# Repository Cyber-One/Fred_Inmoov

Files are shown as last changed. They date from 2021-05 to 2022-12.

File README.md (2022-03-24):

# Fred_Inmoov #


Frequently Re-Engineered Device (FRED)
Fred is a modified InMoov Robot.
You can find the videos showing his contruction here:
https://youtube.com/playlist?list=PLgXTfFM40HqEbnFfhaLPmLv_RS1ZRCilI

In the Official build of InMoov, http://inmoov.fr/
there are two Arduino Mega 2560's located on his back with the I/O distributed using the Nervo Boards available from the online shop in the Inmoov website.
There was also a 8" Lenovo Windows based tablet that running the Java based MyRobotLab http://myrobotlab.org/ that remotely operated the two Arduino Mega 2560's

Because I like to be different, I used the PCA9685 I2C 16 channel PWM driver boards based on the Adafruit servo driver breakout board.
4 of these in various places throughout the robot provide the servo control while reducing the nuber of wires running about the robot.

Lets look at Fred in more detail.
Snapshot - 8

The head is where most of the modifications have been made.
The large Hitech 805BB servo was replaced by a smaller JX Servo PDI6221MG and moved to the back of the skull and turned sideways.
The Jaw servo was relocated turning it over and also moving it sideways.
The eye mechanism was replace with the Dakota76 Advance Eye Mechanism, this has 6 servos with upper and lower eye lids.
With the changes made, there is now enough room in the skull for a Raspberry Pi 4, a PCA9685 Servo Driver and two Switched mode Power Supplies (SMPS) dropping the 20Vdc main power supply down to the 6V for the PCA9685 and 5,1V for the Raspberry Pi.

I used the new neck from the Inmoov.fr site by Gael, this one is far stronger that the other derivative from bob Houstons articultaed neck design.
The downside was because of the modified jaw design and the placement of the SMPS for the PCA9685, I had to extent up the neck mount a bit.
The result is a bit taller neck than normal, this adds close to an inch of height.

Another PCA9685 is located in the back to driver the servos in this area.
Because a lot of these servos are of the larger type, I've used a 20A SMPA to drop the 20Vdc to the 6Vdc for the servos.
I also have a smaller 3A SMPS to power a small 5 port network switch and a second Raspberry Pi located on the back of a 7" LCD touch screen mounted where the original 8" tablet was.


I will be adding two more 20A SMPS, one in each arm to power the servos in the elbow and hands.

One of the most common questions I get about Fred is why am I using 20Vdc in his power system.
The answer to this is to avoid as much power loss as I can.
Power = Volts x Amps.
Volts = Amps x resistance.
Power = Resistance x Amps X Amps.
What a lot of people don't understand is that all wire has a resistance, granted its normally very low, but its there.
The larger the diameter the wire, the lower the resistance, but the longer the wire, the higher the resistance.
If you have a current flowing through a resistance, Ohms Law states there will be a voltage across that resistance.
If you multiply the voltage with the amps flowing you get the power lost in that resistance.  This is power loss.
If you have a servo running 6Vdc at 2.5 Amps, it will be consuming 15 watts of power. 
If you have small wires running a sizable distance you can get quite a voltage drop in the power wires feeding the servo, enough to drop your 6V supply down to 5V or less at the servo this is a 2.5 Watt loss in power that your servo is not getting.
To complicate the matter further, motors will automatically adjust there impedance (think of this as a changing resistance) to get the power they need to rotate the load.
So if the voltage drops, then the motor needs to increase the current to get the same power.
If the impedance drops to the resistance of the servo and there is still not enough power to turn the motor, the result will be a burned out servo motor.
To overcome this problem, I'm keeping the length of the 6Vdc low voltage supply as short as possible, resuding the resistance of those power wires. (Shorter wires, lower resistance, less power lost)
Using a higher voltage, means a lower current for the same amount of power.
At 20Vdc, I end up with 1/3 the amount of current flowing in the supply wires running throught the robot. 
Because the power lost is the wire resistance x Amps squared, that works out to be a significant power saving.
It also means the wires don't have to be overly large.  
Bigger wires also weight more and are not as flexiable.
So there are a few benifits to a higher voltage distribution system.
There is a good table for wire sizes, current capacity and the resistance of the wires at Wikipedia here:
https://en.wikipedia.org/wiki/American_wire_gauge#Tables_of_AWG_wire_sizes

In version 5 of the program I'm using to run Fred, I split the single script up into a number of files and expanded on the comments to help better explain what is happening.
With a bit of luck you will be able to follow along and learn more about how MRL works.
All of the programming I've done is in Python which will make it easier if you want to use this program and need to add to it.

If you have any questions regarding any of the files here, drop into my Discord and ask your questions, hopefully I will be able to answer the questions or implement changes if needed. :-)
https://discord.gg/WzrBUTkthQ

You can download the latest development version of MRL from the MRL website, while your there don't forget to say hello to the developers in the shoutbox.
http://myrobotlab.org/

If your would like to help support this project, then consider Patreon

<a href="https://www.patreon.com/bePatron?u=10744269">Digital-Patreon-Wordmark_WhiteOnFieryCoral-Lg
</a>

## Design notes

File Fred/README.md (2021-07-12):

# Fred Inmoov V5.0 program

Unlike earlier version of Fred's program, this one has split the program up into different sections to make it easier to find parts.
It may yet be broken up into more modular files.
Breaking the project up into a smaller files makes it easier to find and debug issue.
It also helps with designing new features.

Where possible, lots of comment have been placed in the code to help NOOB's learn how MyRobotLab services work and how this section is supposed to work. :-)
It can be advantagous when your trying to use service if you can look up and see how it's ment to be called as well.

<b>Start.py </b>
General start point and is responsible for starting the Graphical User Interface (GUI) and calling all the other sub files required to start up the system.

<b>1_Configuration/</b>
This Folder is where the various configuration files are stored for Fred.
If you are using these scripts for your robot, then this is where you change the config to suit your build.
I've tried to add notes as to what each of the setting do.

<b>Controller.py </b>
This is where the top level controllers are created such as the RasPi service, the Arduino services and the PCA9685 services.

<b>3_Servos/</b>
Because there are so many servos used in an Inmoov build and a modified one like Fred use even more, the servos service creation is broken into multiple files.
I've tried to group servos by physical area of operation, not controller or location of the servo.
For example, the Neck group contains the head Roll, Pitch and Yaw servos, the Roll and Pitch are located below the neck while the Yaw is located in the head. 

<b>IO.py</b>
This is for miscilanous IO devices like the PIR sensor and the Ultrasonic range finders.

<b>Speech.py</br>
This is where the Text To Speech and Speech recognition services are created.

<b>Life.py</b>
This set of routines control the simulation of being alive like the blinking of the eye lids and random movements that simulate a living being.
Because the Life Simulation functions are so complex (mostly to support different types of build) a sub folder was created to break the life functions down into groups of functions.
Later functions will call in and control lower level functions so as to make coordinated moves, like moving the eyes and head to look at an object.

<b>Gestures.py</b>
Any scripts of movements such as shaking the head as a no, or nodding the head as a yes, that may be called by the ProgramAB are scripted here.
Think of the Life functions as involuntary functions and Gestures as voluntary functions, normally called from the brain (ProgramAB)

<b>Brain.py</b>
This is where the simulated AI lives. :-)
For now, this is ProgramAB, a program that runs Artificial Inteligents Markup Language (AIML) files commonly refered to as Alice Bot.

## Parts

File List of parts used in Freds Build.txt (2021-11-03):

I get asked a lot about where I get the STL files I used in the building of Fred.
Below is a list of the different locations for parts I've printed that are non-standard Inmoov parts.
All other parts not listed are on the official Inmoov site
http://www.inmoov.fr/

https://www.thingiverse.com/thing:2394098
InMoov - Accessible skull with continous forehead by dix238.

http://www.thingiverse.com/thing:992918
Modified InMoov head by monnerby.

http://www.thingiverse.com/thing:3395654
InMoov Neck Head Bracket Another Redesign v2 by richardtracy

http://www.thingiverse.com/thing:2335838
InMoov LowBackSkull & Gear remix by richardtracy

http://www.thingiverse.com/thing:1581955
InMoov - Low Back Skull / Neck Joint - Modification by dix23.

https://www.thingiverse.com/thing:1636086
InMoov Face less holes by juergm.

http://www.thingiverse.com/thing:2062472
Raspberry Pi 2 Stacking System by TafThorne
This was modified to let me use PCB standoffs.

https://www.thingiverse.com/thing:2548952
InMoov - Advanced Eye Mechanism by Dakota76.

Alexinator40
Remixed from
http://www.thingiverse.com/thing:3395654
InMoov Neck Head Bracket Another Redesign v2 by richardtracy
Remixed from
http://www.thingiverse.com/thing:1581955
InMoov - Low Back Skull / Neck Joint - Modification by dix23
Remixed from
http://www.thingiverse.com/thing:992918
Modified InMoov head by monnerby.
Remixed from
http://www.inmoov.fr/
Created by Gael Langevin

AT30_SMPS.STL https://www.dropbox.com/s/qasvv97k4j6kot5/AT30_SMPS.stl?dl=0
Created by Cycber_One

PCA9685_Mount.STL https://www.dropbox.com/s/vjgidlmbo2zt9v8/PCA9685_Mount.stl?dl=0
Created by Cyber_One

http://www.thingiverse.com/thing:2770920
Aldi Xfinity and Ryobi (south africa) battery connector by Stoney

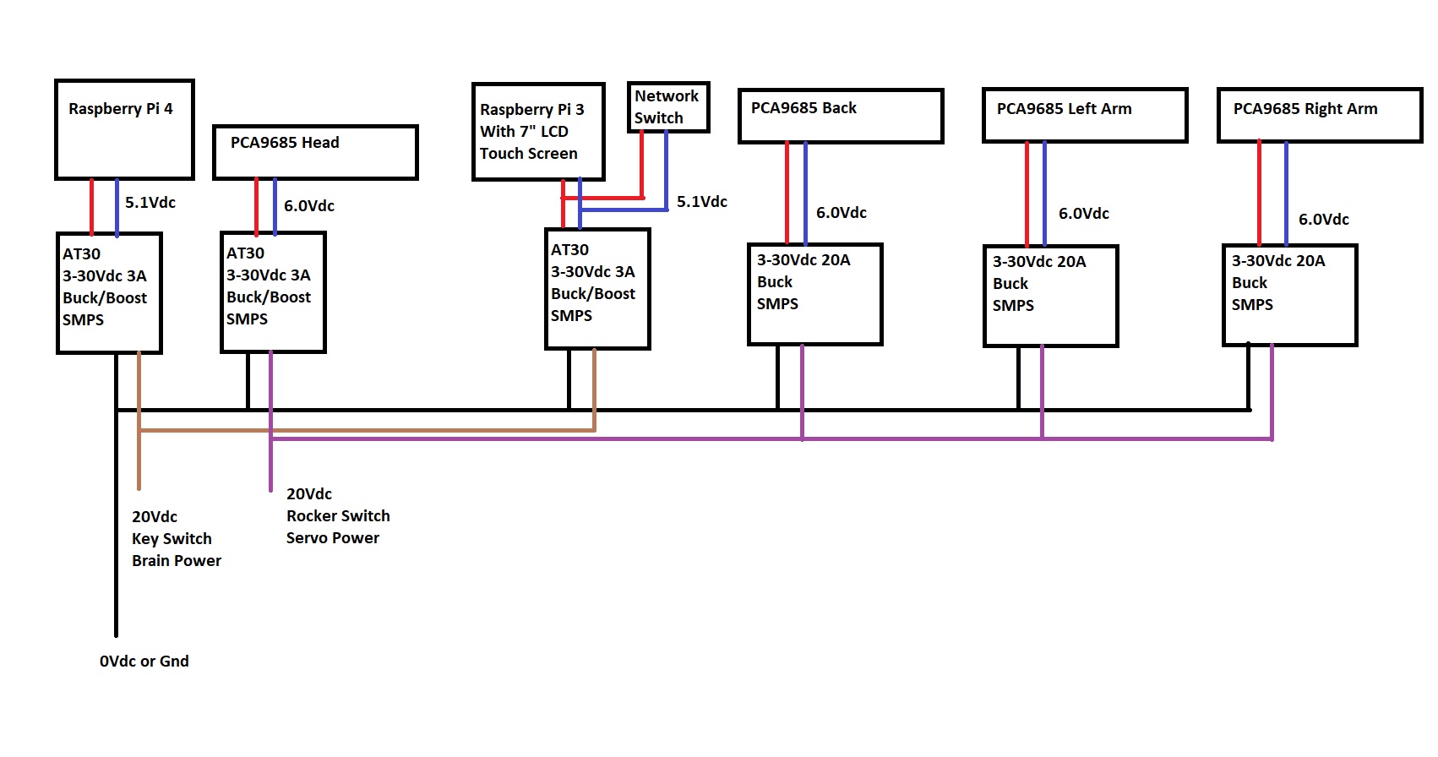
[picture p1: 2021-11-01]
Parts/Power System Layout.jpg

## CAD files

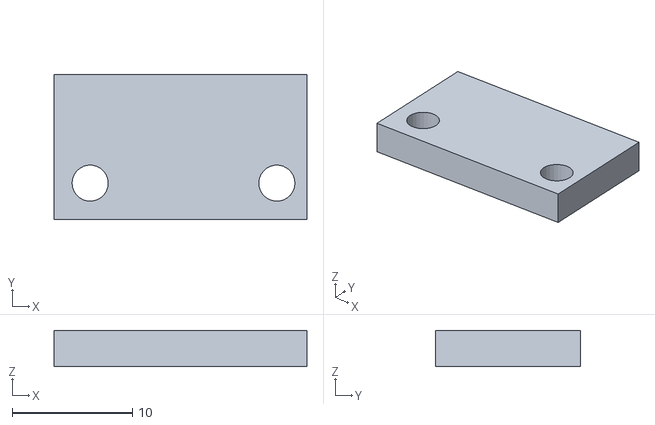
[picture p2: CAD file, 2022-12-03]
Parts/MPU6050_Mount.stl
21.0 x 12.0 x 3.00

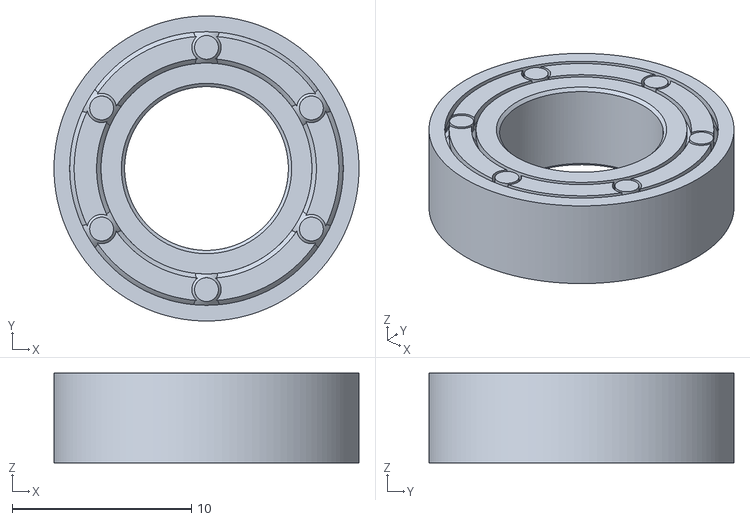
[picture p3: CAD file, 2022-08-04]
Parts/Bearing_689_Hv1_9x17x5.stl
17.0 x 17.0 x 5.00

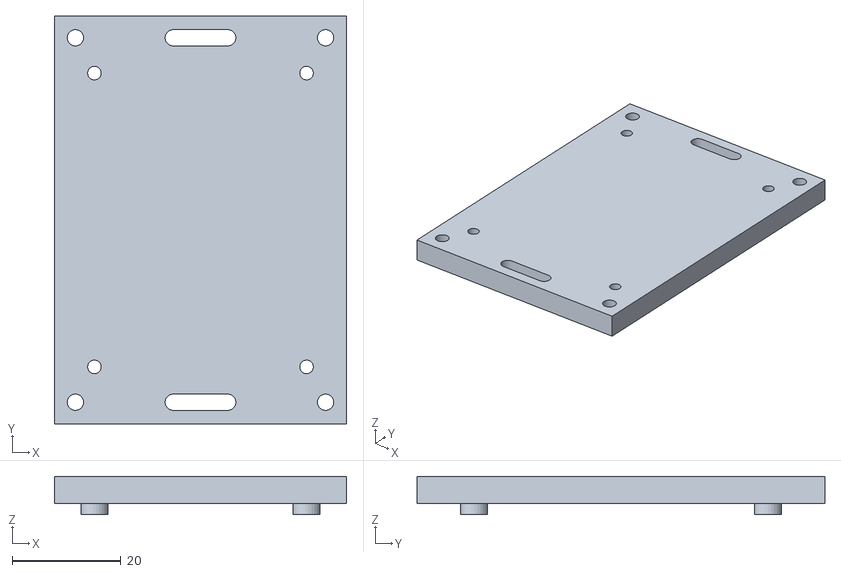
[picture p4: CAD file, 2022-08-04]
Parts/20A_SMPS_Mount_V2.stl
53.7 x 75.0 x 7.00

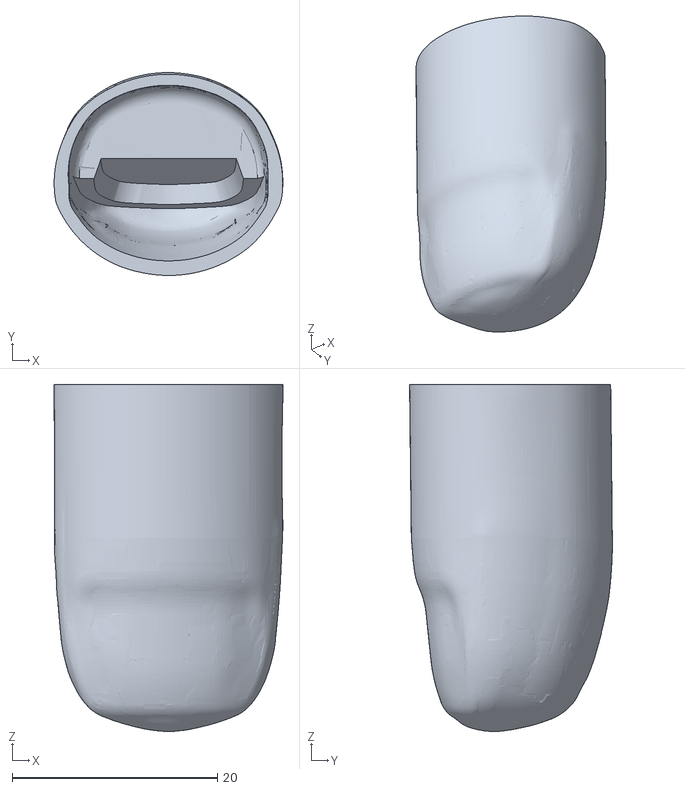
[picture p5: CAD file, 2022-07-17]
Parts/Thumb_TipV2.stl
22.3 x 19.8 x 33.8

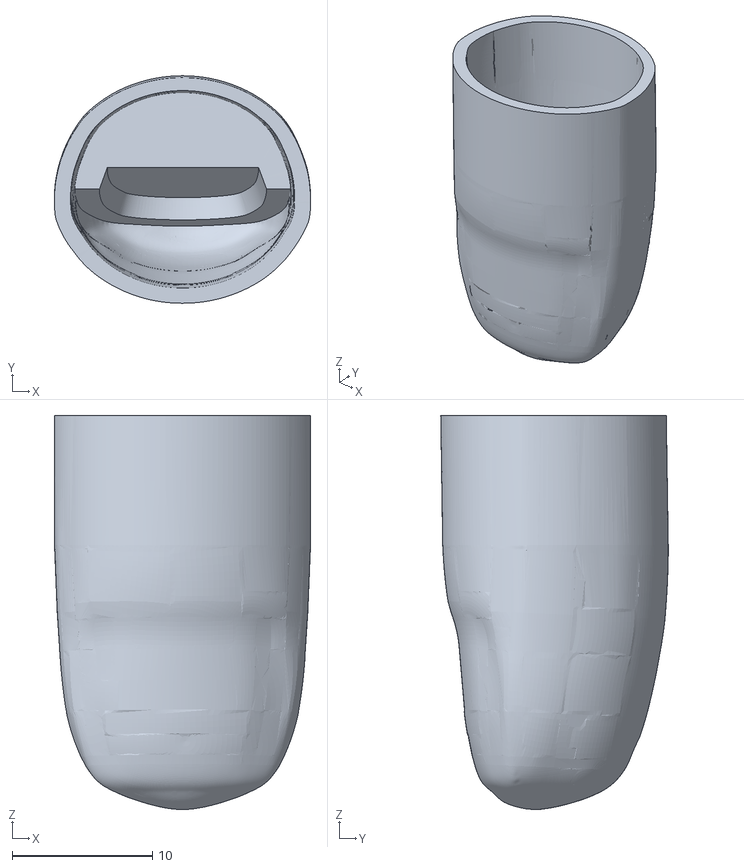
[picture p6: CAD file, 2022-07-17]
Parts/Finger_TipV1_with_shallow_magnet_hole.stl
18.3 x 16.2 x 28.1

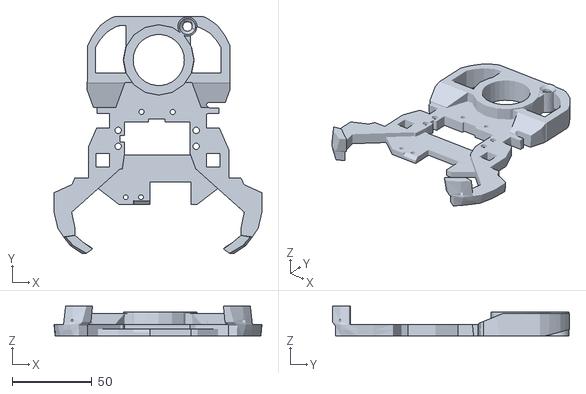
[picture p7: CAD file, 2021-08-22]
Parts/RayFileFixed.stl
130.6 x 149.1 x 18.6

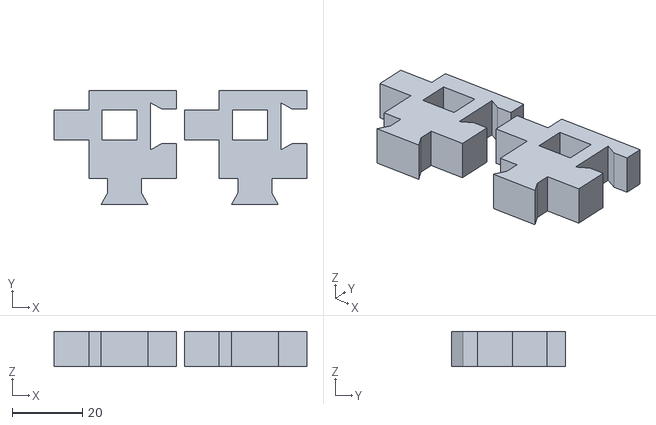
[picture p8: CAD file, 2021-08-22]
Parts/Calibrator.stl
72.2 x 32.5 x 9.99

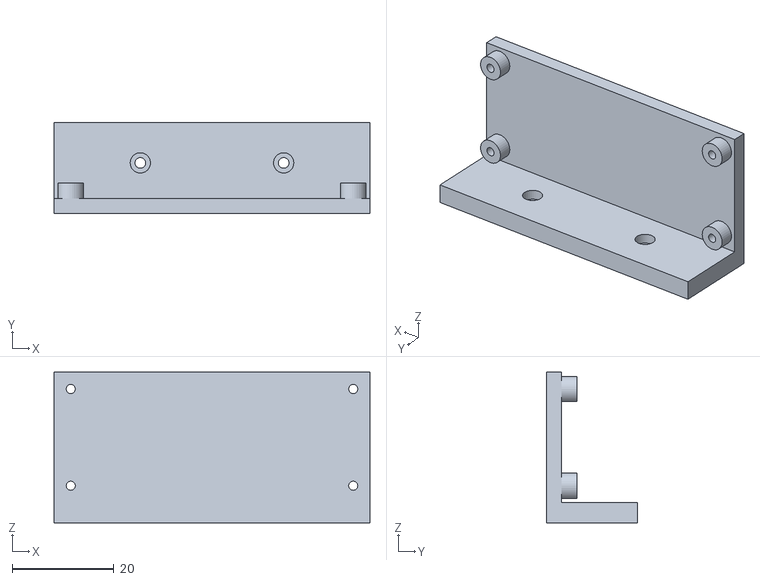
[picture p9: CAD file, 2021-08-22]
Parts/PCA9685 Mount v2.stl
62.2 x 18.0 x 29.7

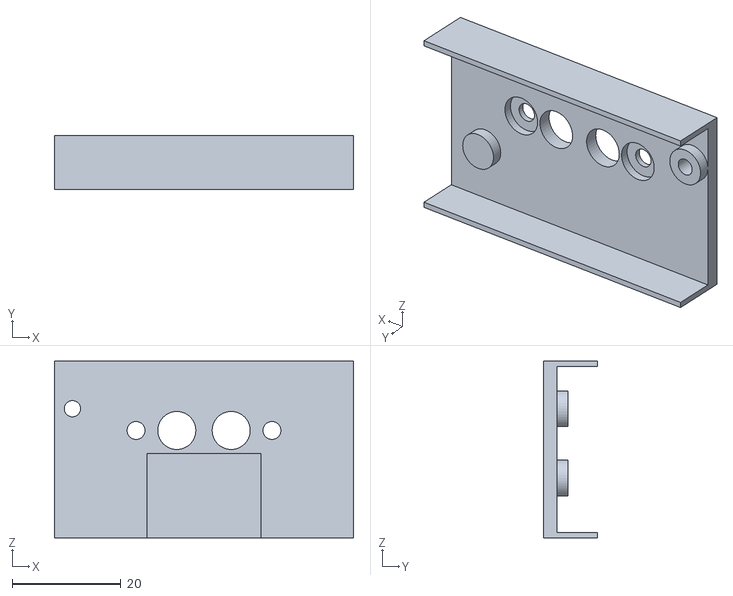
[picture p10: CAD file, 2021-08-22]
Parts/AT30 Buck-Boost Mount v8.stl
55.0 x 10.0 x 32.5

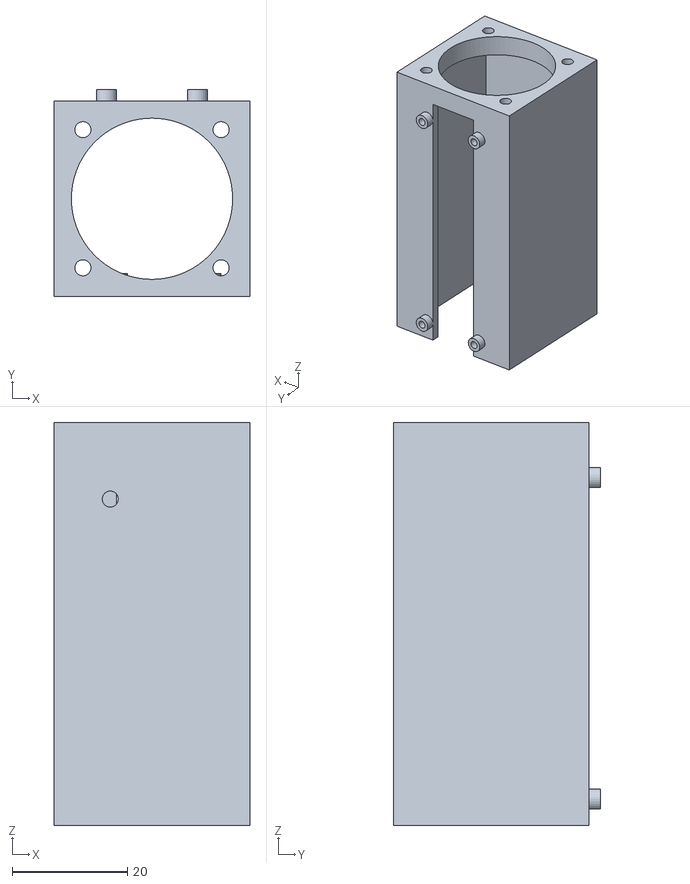
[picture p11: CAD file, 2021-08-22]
Parts/AT30_PCA9685.stl
34.0 x 36.0 x 70.0

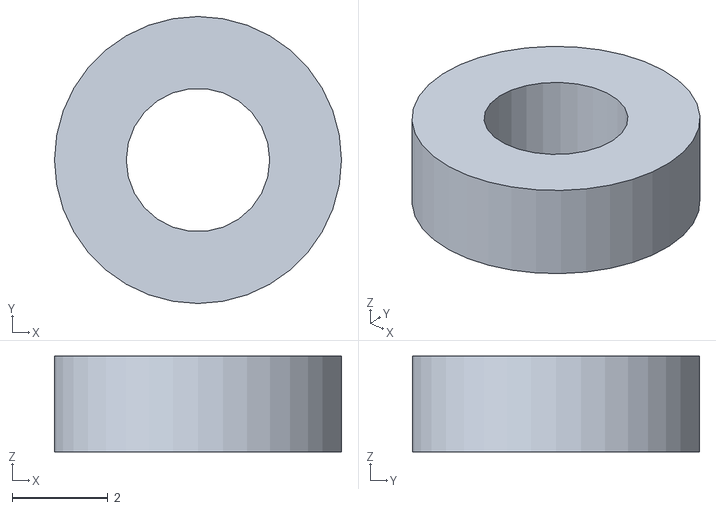
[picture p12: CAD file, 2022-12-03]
Parts/Washer.stl
6.00 x 6.00 x 2.00

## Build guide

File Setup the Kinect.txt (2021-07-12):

Accessing the Xbox 360 Kinect using the Raspberry Pi

Once you have the unit connected and up and working, you can access the images. 
First, you'll need to install a library called freenect, which will make it very easy to access both the regular and depth images from the Kinect 360. 

To do this, type 
sudo apt-get install freenect
You'll also need a library to allow you to access freenect from Python; to get this, type 
sudo apt-get install python-freenect
Once you have the libraries installed, you'll also need to install a library that will allow you to access the images on the Raspberry Pi graphics system. 
To do this, type 
sudo apt-get install libgl1-mesa-swx11

You can check to see if everything is working by opening a vncserver window and typing 
freenect-glview
You should see something like this:
https://static.packt-cdn.com/products/9781786467966/graphics/image_03_048.jpg

Using this in MyRobotLab (MRL) is also not that hard.
After starting MRL, launch the OpenCV service then select the Kinect as the camera source and click on Capture.

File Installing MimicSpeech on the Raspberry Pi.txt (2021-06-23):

Before we can use Mimic speech with MyRobotLab on the Raspberry Pi, we first need to install it.
The compiled executable is installed with MRL for windows, but not for the ARM based linux install used on the Raspberry Pi.
The following link is video showing the below steps :-)
https://youtu.be/OSbqlRWYBkQ
 
For this I'm using the instruction from the MycroftAI github site:
https://github.com/MycroftAI/mimic1
 
There are a few packages required to allow us to setup Mimic speech, so lets get those installed first.
From the terminal window, you will need to execute the following command.
 
sudo apt-get install gcc make pkg-config automake libtool libasound2-dev
 
For the NOOBs out there.
sudo is the command Super User Do
apt-get is the Aptidtude Package manager that we use to install pre-compiled programs within the Debian environment.
install is the command for the apt-get, the rest of the line are a list of packages to install.
 
The good news is, if any or all of the packages are already installed, then this command will check and make sure they are current and up to date, if they aren't installed, then it will download and install them for you.
 
Now thats done, we need to download thesource files for Mimic Speech.
This is easywith the following command
 
git clone https://github.com/MycroftAI/mimic1.git
 
This will create a new sub directory which we will need to change into
 
cd mimic1
 
Now it's just about garunteed that some of the dependencies won't be installed, so lets deal with that now
In the mimic1 directory, there is are shell scripts that will do all the hard work for you :-)
 
./dependencies.sh --prefix="/usr/local"
./autogen.sh
./configure --prefix="/usr/local"
 
Now we get to build the Mimic program tailored to the Raspberry Pi ARM based processor
to do that we execute the command
 
make
 
this is gonna take a while, Time for a cupper :-)
 
When it does finnaly finish, we need to check it all went acording to plan.
So run the following
 
make check
 
That should com back all green with everything having been built ok.
 
Time for a test :-)
ececute to following line
 
./mimic -t "Hello. Doctor. Name. Continue. Yesterday. Tomorrow."
 
Note, the . at the start tells the terminal window, theprogram your trying to run is in this directory, if you don't have that there, it won't find our brand new program.
Unlike windows, programs in linux don't need to have file extentions in the name :-)
 
There are a few voices bundelled with Mimic Speech, to get a list of them, run the command
 
./mimic -lv
 
To use a different voice when starting a speech from theterminal try:
 
./mimic -t "Hello" -voice slt

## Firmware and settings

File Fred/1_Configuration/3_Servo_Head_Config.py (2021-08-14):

##############################################################
#                                                            #
# Program Code for Fred Inmoov                               #
# Of the Cyber_One YouTube Channel                           #
# https://www.youtube.com/cyber_one                          #
#                                                            #
# This is version 5                                          #
# Divided up into sub programs                               #
# Coded for the Nixie Version of MyRobotLab.                 #
#                                                            #
# Running on MyRobotLab (MRL) http://myrobotlab.org/         #
# Fred in a modified Inmmov robot, you can find all the      #
# origonal files on the Inmoov web site. http://inmoov.fr/   #
#                                                            #
# 3_Servo_Head_Config.py                                     #
# This is where the configuration settings live for the      #
# varoius controllers.                                       #
#                                                            #
##############################################################
print "Creating the Servo Head Config"
##############################################################
#                                                            #
# Servo Head Group                                           #
#                                                            #
##############################################################

# Each servo has a number of parameters that need to be setup 
# before it can be used, these include where it's attached 
# and how far it can be moved.
# In the InMoov scripts and services, it assumes that your 
# servos are connected to one of the Arduino Mega 2560's.
# In the case of Fred using the PCA9685, this is not the case.
# In this config, the only assumption I will make is that the
# Servo will be attaches somewhere :-)
# The default values will be one of our controllers.
# "arduinoLeft", "arduinoRight", "arduinoNano", "Head", 
# "Back", "RightArm", "LeftArm".
# If a new controller is released or more servos are added, 
# then add it to this list and to each of the servos in the 
# related Servo.py file.  In this case 1_Servos_Head.py
# Comments after the setting are for a Nervo Boards based 
# InMoov configuration as listed on the InMoov web site.
# In some cases, the direction of travel is sometime in the
# oposite direction to what we need.  In this case, swap the
# Min and Max pos, this will swap the direction to what we need.

# The Jaw
# There are a few different variations on how the mechanics
# of this works, but essentially, rotating the servo closes
# the jaw while rotating it the other way opens it.
EnableJawServo = True # True or False
# This is the controller the Jaw Servo is attached to
JawAttachment = "Head"          # "arduinoLeft"
# The controller will have a number of pis, this is the pin 
# this servo is connected to.
JawPin = 9                      # 26
# The is the value from testing where the Jaw is all the way closed.
JawMinPos = 70                  # 10
# This is the value from testing where the jaw is all the way open
JawMaxPos = 140                 # 25
# This is the speed that the moves at. -1 is no speed limit,
# the jaw will move as fast as possible.
JawVelocity = -1                #


# In the original design, there are only two servos for the
# eyes, the X and Y servos.  Later, another servo was added
# for eye lids.
# In the Advanced Eye Mech by Dakota76, there are 6 servo used

# The Right Eye X-Axis (Left / Right motion)
EnableRightEyeX = True
RightEyeXAttachment = "Head"    # "arduinoLeft"
RightEyeXPin = 15               # 22
RightEyeXMinPos = 0             # 60
RightEyeXMaxPos = 180           # 120
RightEyeXVelocity = -1          #

# The Right Eye Y-Axis (Up / Down Motion)
EnableRightEyeY = True
RightEyeYAttachment = "Head"    # "arduinoLeft"
RightEyeYPin = 14               # 24
RightEyeYMinPos = 0             # 60
RightEyeYMaxPos = 180           # 120
RightEyeYVelocity = -1          #

# The Left Eye X-Axis (Left / Right motion)
# The Advance Eye Mech by Dakota76 has servos for both eyes.
EnableLeftEyeX = True
LeftEyeXAttachment = "Head"     # Not Present
LeftEyeXPin = 13                #
LeftEyeXMinPos = 0              #
LeftEyeXMaxPos = 180            #
LeftEyeXVelocity = -1           #

# The Left Eye Y-Axis (Up / Down Motion)
EnableLeftEyeY = True
LeftEyeYAttachment = "Head"     # Not Present
LeftEyeYPin = 12                #
LeftEyeYMinPos = 180            #
LeftEyeYMaxPos = 0              #
LeftEyeYVelocity = -1           #

# The Right Upper Eye Lid
EnableRightUpperEyeLid = True
UpperREyeLidAttachment = "Head" # "arduinoRight"
UpperREyeLidPin = 11            # 13
UpperREyeLidMinPos = 150        # 60
UpperREyeLidMaxPos = 45         # 120
UpperREyeLidVelocity = -1       #
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

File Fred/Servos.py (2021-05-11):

##############################################################
#                                                            #
# Program Code for Fred Inmoov                               #
# Of the Cyber_One YouTube Channel                           #
# https://www.youtube.com/cyber_one                          #
#                                                            #
# This is version 5                                          #
# Divided up into sub programs                               #
# Coded for the Nixie Version of MyRobotLab.                 #
#                                                            #
# Running on MyRobotLab (MRL) http://myrobotlab.org/         #
# Fred in a modified Inmmov robot, you can find all the      #
# origonal files on the Inmoov web site. http://inmoov.fr/   #
#                                                            #
# Servos.py                                                  #
# This file is to start all the servos used in the Robot     #
#                                                            #
##############################################################
print "Starting the various Servos Services"

##############################################################
#                                                            #
# Servo Head Group                                           #
#                                                            #
##############################################################

print "-Head Group"

if EnableJawServo == True:
    print "--The Jaw"
    # The Servo service is designede to operate a number of
    # different types of servos via different controllers
    # while providing a common interface for your robot.
    # Before we can use a servo, we must first create the
    # servo object by using the Runtime service and the 
    # createAndStart function, passing in the Name we want to
    # call our new servo service as well as the type of 
    # service, in this case "Servo".
    # We then assign this new object to a variable.
    # In this example, we are assigning a Servo Service to 
    # the variable Jaw
    Jaw = Runtime.createAndStart("Jaw", "Servo")
    # Once we have a Servo service, we need to attach it to 
    # a controller on our system.  There can be more than one 
    # controller or even types of controllers within the 
    # system, so we need to tell the service where to find 
    # the controller and what pin to connect ther servo 
    # service to.  For that we use the attach method.
    # This method takes two parameters, the first is the 
    # service object.
    # The second parameter is the pin on the controller that 
    # the servo will be attached to.
    # Because we have a number of options for the controller 
    # service, and we want to make is easy to configure, we 
    # will set a config string with the service names and 
    # then select the service based on that name from a list 
    # of possible service we are likely to use.
    if JawAttachment == "Head":
        Jaw.attach(Head, JawPin)
    if JawAttachment == "Back":
        Jaw.attach(Back, JawPin)
    if JawAttachment == "RightArm":
        Jaw.attach(RightArm, JawPin)
    if JawAttachment == "LeftArm":
        Jaw.attach(LeftArm, JawPin)
    if JawAttachment == "arduinoLeft":
        Jaw.attach(arduinoLeft, JawPin)
    if JawAttachment == "arduinoRight":
        Jaw.attach(arduinoRight, JawPin)
    if JawAttachment == "arduinoNano":
        Jaw.attach(arduinoNano, JawPin)
    # When you install your servo into your robot, you may 
    # find that the servo turns to far and has to potential 
    # of damaging your robot.  In this case you will want to 
    # limit how far the servo turns.   To do this we use the 
    # set Min/Max method.  This method while still working is 
    # being depreciated, it is suggested to use the map 
    # method instead.
    Jaw.setMinMax(JawMinPos, JawMaxPos)
    # A lot of servos will have a 180 degree range of motion.
    # however there are some with more range and others with 
    # less range, the servo service cannot tell these types 
    # apart, the solution is to Map them :-)
    # If you have a 270 degree servo, the same PWM signal 
    # range for the 180 dgree servos will rotate 270 degree.
    # What we can do is Map the 0 - 180 to the 0 - 270 degrees
    # In this case, we would map the 0 - 270 as the input to 
    # the 0 - 180 on the output. Then when you adjust the 
    # output by 90 degrees the servo will turn 90 degrees.
    #Jaw.map(0, 100, JawMinPos, JawMaxPos)
    # The Rest position is a pre-programmed position for the 
    # servo to move to when you call the rest method.
    Jaw.setRest(JawRestPos)
    # On occasion you may need to reverse the direction of a 
    # servo. You may have an arm on each side of the robot, 
    # where 90 degree it pointing forward, but 0 degrees has 
    # one arm move up while the other moves down.  In this 
    # case you may want both servo to mover the arms down.
    # What you will want to do is Invert the direction of one 
    # of the servos so that both are down at 0 degrees.
    # Setting the setInvert to True will invert the servo.
    Jaw.setInverted(False)
    # Without any speed control, when you change a servos 
    # position, the servo will try and rotate to the new 
    # position as fast as it can.  This can at times be 
    # undesirable, resulting in your whole robot shaking or 
    # worse falling over causing damage.  The speed at which 
    # the servo rotate can limited or controlled by sending a 
    # series of position updates between the current position 
    # and the target position.  The rate of rotation is set 
    # in degrees per second.  
    # A value of -1 disables speed control.
    Jaw.setSpeed(-1)
    # The Servo service has a feature where it will disable a 
    # servos, saving power and potentially preventing the 
    # servo from burning out.  This feature can be disabled 
    # when disabling the servo would be bad.
    Jaw.setAutoDisable(True)
    # The rest method will send to servo to the pre-programmed 
    # position as set by the setRest method or if not set, to 
    # the default position of 90 degrees.
    #Jaw.rest()
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

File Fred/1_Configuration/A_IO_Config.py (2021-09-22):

##############################################################
#                                                            #
# Program Code for Fred Inmoov                               #
# Of the Cyber_One YouTube Channel                           #
# https://www.youtube.com/cyber_one                          #
#                                                            #
# This is version 5                                          #
# Divided up into sub programs                               #
# Coded for the Nixie Version of MyRobotLab.                 #
#                                                            #
# Running on MyRobotLab (MRL) http://myrobotlab.org/         #
# Fred in a modified Inmmov robot, you can find all the      #
# origonal files on the Inmoov web site. http://inmoov.fr/   #
#                                                            #
# A_IO_Config.py                                             #
# This is where the configuration settings live for the      #
# varoius devices that don't fit in the other catagories.    #
#                                                            #
##############################################################
print "Creating the Input/Output Config"

##############################################################
#                                                            #
# The PIR                                                    #
#                                                            #
##############################################################
# Passive Infra Red (PIR) works on the principle that a 
# warm body emits Infra Red (IR) light. The level of this 
# light can indicate the current temperature.
# PIR sensors, use a single sensing element to measure the 
# ambient IR level.
# By using a segmented lens in front of the sensor, there 
# will be areas where the sensor can not see the IR 
# levels, and areas where it is amplified.  
# As a warm body such as a person moves from one area to 
# another, there is a large change in the IR levels 
# detected, when this change occurs the output of the PIR 
# sensor is turned on.
EnablePIR = True
PirAttachment = "arduinoNano"               # "arduioLeft"
PirPin = 2                                  # 23

##############################################################
#                                                            #
# The Ultra-Sonic Range Sensors                              #
#                                                            #
##############################################################
# Ultrasonic sensors emit a pulse of high frequency sound normally
# 8 cycles at a frequency the we can not hear.
# They then wait for the reflected sound to be detected.
# The time taken for the sound pulse to travel to an object and be
# reflected back can be timed and give a reasonable indication of
# the distance the object is away from the sensor.
# The speed of sound in air is about 343 metres per second 
# or 1,235 km/h; 1,125 ft/s; 767 mph.
# The speed of sound however will vary with temperature.
# Speed = 331.3 + (0.606 * airTemp) m/s
# Our robot use a Ultrasonic module to do the above, but we
# need to handle the time measurement.
# MRL offloads this to the Arduino, It starts the pulse
# transmission using the transmit pin, the times how long it
# takes for the receive pin to be pulsed high.
# From there it can do the math to get a distance.
# Pin 1 is used for the Transmit of the pulse.
# Pin 2 is used for the receive of the return pulse.
EnableLeftUltrasonic = True                 #
LeftUltrasonicAttachment = "arduinoNano"    # "arduioLeft"
LeftUltrasonicPin1 = 10                     # 64
LeftUltrasonicPin2 = 9                      # 63

EnableRightUltraSonic = True                #
RightUltrasonicAttachment = "arduinoNano"   # "arduioRight"
RightUltrasonicPin1 = 12                    # 64
RightUltrasonicPin2 = 11                    # 63

# Time between Pings in milli-seconds.
PingTime = 1000
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

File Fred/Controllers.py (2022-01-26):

#################################################################
#                                                               #
# Program Code for Fred Inmoov                                  #
# Of the Cyber_One YouTube Channel                              #
# https://www.youtube.com/cyber_one                             #
#                                                               #
# This is version 5                                             #
# Divided up into sub programs                                  #
# Coded for the Nixie Version of MyRobotLab.                    #
#                                                               #
# Running on MyRobotLab (MRL) http://myrobotlab.org/            #
# Fred in a modified Inmmov robot, you can find all the         #
# origonal files on the Inmoov web site. http://inmoov.fr/      #
#                                                               #
# Controllers.py                                                #
# This file isto start any major controllers                    #
# we might need.                                                #
#                                                               #
#################################################################
print "Starting the various Controllers"

#################################################################
# Load the configuration for the Controllers.                   #
#################################################################
execfile(RuningFolder+'/1_Configuration/2_Controller_Config.py')

#################################################################
# Start the Raspberry Pi service.                               #
# The core of the Fred InMoov build,                            #
# is the Raspberry Pi 4 (Raspi4) Single Board Computer (SBC)    #
# This small low cost computer is not powerful enough to run    #
# everything, but there is no reason why we can't have more     #
# than one Raspi4 installed in Fred.                            #
# The first one is installed in the top of the head, but we     #
# can add one or two more in the back at a later date and       #
# split the processing up.                                      #
# The Raspi4 has two I2C ports built in,                        #
# Port 0 is used for the microSD card,                          #
# while Port 1 is available for us to use.                      #
#################################################################
if EnableRaspberryPi == True:
    print "-Starting the Raspberry Pi Service"
    raspi = Runtime.start("raspi","RasPi")

#################################################################
# If you were to run the two Arduino Mega 2560 as used in a     #
# standard build, this is also where you would start the        #
# services.  Again each of the Arduino Mega 2560 have an I2C    #
# Port 0.  To use these remove the # from in front of the       #
# lines needed.  Also make sure the USB port is listed          #
# correctly and the MRL_COMM is installed on each arduino       #
# that you have installed into your robot.                      #
#################################################################
# For the Left Arduino Mega 2560                                #
#################################################################
if EnableArduinoLeft == True:
    print "-Starting the Arduino Mega 2560 Left Service"
    arduinoLeft = Runtime.start("arduinoLeft","Arduino")
    arduinoLeft.setBoardMega()
    arduinoLeft.connect(ArduinoLeftComPort)

#################################################################
# For the Right Arduino Mega 2560                               #
#################################################################
if EnableArduinoRight == True:
    print "-Starting the Arduino Mega 2560 Right Service"
    arduinoRight = Runtime.start("arduinoRight","Arduino")
    arduinoRight.setBoardMega()
    arduinoRight.connect(ArduinoRightComPort)

#################################################################
# Start the Arduino Nano connected using /dev/ttyUSB0           #
# In the Fred build, I'm using an Arduino Nano for the two      #
# Ultrasonic Sensors and the PIR sensor.                        #
# The Arduino also has an I2C Port 0 if we need to use it.      #
#################################################################
if EnableArduinoNano == True:
    print "-Starting the Arduino Nano Service"
    arduinoNano = Runtime.start("arduinoNano","Arduino")
    arduinoNano.setBoardNano()
    arduinoNano.connect(ArduinoNanoComPort)

#################################################################
# After hearing some builders were installing a second Arduino  #
# Nano in the head for the NeoPixels in the eyes, I added in    #
# support for it :-)                                            #
#################################################################
if EnableArduinoNano2 == True:
    print "-Starting the Arduino Nano 2 Service"
    arduinoNano2 = Runtime.start("arduinoNano2","Arduino")
    arduinoNano2.setBoardNano()
    arduinoNano2.connect(ArduinoNano2ComPort)

#################################################################
# To assist in performing a sanity test, the following function #
# will return either the CurrentState or False based on the     #
# name of the configured service for I2C supporting services.   #
#################################################################
def TestI2CControllerExists(ControllerName, CurrentState):
    if ((ControllerName == "raspi" and EnableRaspberryPi)
        or (ControllerName == "arduinoNano" and EnableArduinoNano) 
        or (ControllerName == "arduinoNano2" and EnableArduinoNano2) 
        or (ControllerName == "arduinoLeft" and EnableArduinoLeft) 
        or (ControllerName == "arduinoRight" and EnableArduinoRight)):
        return(CurrentState)
    else:
        return(False)

#################################################################
# To assist in performing a sanity test, the following function #
# will return either the CurrentState or False based on the     #
# name of the configured service for Arduino supporting         #
# services.                                                     #
#################################################################
def TestArduinoControllerExists(ControllerName, CurrentState):
    if ((ControllerName == "arduinoNano" and EnableArduinoNano) 
        or (ControllerName == "arduinoNano2" and EnableArduinoNano2) 
        or (ControllerName == "arduinoLeft" and EnableArduinoLeft) 
        or (ControllerName == "arduinoRight" and EnableArduinoRight)):
        return(CurrentState)
    else:
        return(False)
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

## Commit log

2021-02-06 Fred with his first Arduino
    The Arduino is used for the PIR sensor and 2 x Ultrasonic sensors
2021-02-15 Bug fix in Servos and bug chase in Life
    [Servos.py]
2021-02-17 Added Sleep Timer
2021-02-18 Added Configuration.py
    Set it up to make it easy to configure the program.
    Controller.py is done, next is the servos.
2021-02-21 Updated Servo.py
2021-02-21 Add RollStomach Servo Control
2021-02-23 Splitting up the servos commands
2021-02-25 Finished splitting up the servos
2021-04-17 Adjusting Calibrations
2021-04-17 Update 5_Servo_Torso_Config.py
    Added to the comments to better describe the functions of different servo motors.
2021-04-26 Added velocity config for the head
    Also improved commenting
2021-05-01 Bug Fixes and documentation
    [1_Servos_Head.py, 3_Servo_Head_Config.py, C_Life_Config.py]
2021-05-02 Update 1_Servos_Head.py
    Change Head servo's to use 0-100 percent of range.
2021-05-03 Inverting Eyelid Motion
    Making it % open, so 0% is closed, 100% is open
    [3_Servo_Head_Config.py]
2021-05-05 Update Velocity to Speed
2021-05-07 Added support for reversing and MaxSpeed
    [7_Servo_LeftArm_Config.py]
2021-05-07 Update 3_Servo_Head_Config.py
    Just a bit of an error :-)
    [3_Servo_Head_Config.py]
2021-05-09 Working on the Ultrasonic services
2021-05-11 Fixed servo naming convention for the Stomach servo for Pitch control
    [5_Servo_Torso_Config.py, Servos.py]
2021-05-12 Added Look framework
2021-05-14 Correct Rest Pos in the head Add to LookControl
    [3_Servo_Head_Config.py]
2021-05-16 Fix Rest Pos on Servos
    [1_Servos_Head.py, 3_Servo_Head_Config.py, 4_Servo_Neck_Config.py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]
2021-05-17 Updated Servos Right Hand
2021-05-17 Update Servo Control
2021-05-17 Fixing small issue :-)
    [1_Servos_Head.py, 4_Servo_Neck_Config.py]
2021-05-19 Reduce the number of print statement for debugging
2021-05-19 Remove another debug print
2021-05-21 Solving the NeoPixels bug
    [C_Life_Config.py]
2021-05-24 Add battery Monitoring
2021-05-25 Move the MPU6050 to IO out of controllers
    The MPU6050 is a input device returning the current orientation of the device.
    It is not a controller.
    Also moved the starting of the IO devices to before the servos.
2021-05-27 Bug hunt in Manticore
    [A_IO_Config.py]
2021-05-28 Working on Multiple Battery Monitoring
2021-05-29 Adding Battery Monitor Features
2021-05-29 Update IO.py
    Adding to the Battery Monitor program
2021-05-29 testing Battery Monitor functions
2021-05-29 I think I have the Battery Level Working
2021-05-29 Fix a bug in the NeoPixel sections
    [C_Life_Config.py]
2021-06-05 Update and correct documentation
    [A_IO_Config.py]
2021-07-03 Added support for second Arduino Nano
    I have not yet enabled the second Arduino for Servo control, but I will in the future.
    You could in theory put one in the head and run the servos there.
2021-07-04 Add support for Arduino Nano 2
2021-07-10 Create Tips for getting sound working in Java on the Raspberry Pi.txt
2021-07-12 Create Setup the Kinect on the Raspberry Pi.txt
2021-07-17 Create the Framework.
2021-08-14 Update IO.py
    Fixed NeoPixels to support new method of attachment.
2021-08-14 Added Lateral Jaw and EyeBrow servos
2021-08-20 Bug Fix found during recording
    [1_Servos_Head.py]
2021-08-22 Added custom STL files
    [AT30 Buck-Boost Mount v8.stl, AT30_PCA9685.stl, Calibrator.stl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]
2021-08-26 Add Sanity check for Arduino Controllers
2021-08-28 Adding Bug fixes and comment improvements
    [A_IO_Config.py]
2021-08-28 Building the Framework for a distributed system
2021-11-01 Create Power System Layout.jpg
2022-01-22 Bug fix.
    Typo, used a capital S instead of a lowercase s
    [Controllers.py]
2022-07-17 New Parts
    [Finger_TipV1_with_shallow_magnet_hole.stl, Thumb_TipV2.stl]
